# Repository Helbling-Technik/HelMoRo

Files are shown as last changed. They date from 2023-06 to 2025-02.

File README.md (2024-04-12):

# HelMoRo Hardware Repo

This repo includes all the Hardware files referenced on the Documentation Website.
You'll find the Website under [https://helbling-technik.github.io/HelMoRo/](https://helbling-technik.github.io/HelMoRo/)

Additionally all the Helmoro Documentation Markdown files that are used to produce the Documentation Webpage are stored here under the '/doc' folder.
There you'll find another [README.md](/docs/README.md) specifically about the website.

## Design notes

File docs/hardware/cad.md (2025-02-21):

# CAD 

## Downloads

In addition to the [Fusion 360 Widget ](https://helbling2.autodesk360.com/shares/public/SHd38bfQT1fb47330c99f726a386eb5b24d0) (HelMoRo with Raspberry Pi 5), we provide the model in the following formats:

- [Solidworks 2021](https://github.com/Helbling-Technik/HelMoRo/tree/master/cad/solidworks) 
- [STEP](https://github.com/Helbling-Technik/HelMoRo/tree/master/cad/step) 
- [STL](https://github.com/Helbling-Technik/HelMoRo/tree/master/cad/stl) 

Some files extend the file limit of 100 Mb, and therefore, we use [GitHub LFS](https://git-lfs.com/) (Large File Storage) to manage these large files effectively. Instructions how to use GitHub LFS can be found under [Collaboration](../../collaboration#accessing-the-repository).

## Naming Convention

The file names are in the following format:
**HEL-XX-UUYYY-RR.xyz**

- **HEL**: This prefix represents the client.
    <div style="margin-left: 20px;">
        <strong>&nbsp;&nbsp;&nbsp;HEL:</strong> Helbling (internal project)<br>
    </div>

- **XX**: This section indicates the type of the CAD file.
    <div style="margin-left: 20px;">
        <strong>&nbsp;&nbsp;&nbsp;01:</strong> Main assembly<br>
        <strong>&nbsp;&nbsp;&nbsp;03:</strong> Sub-assembly<br>
        <strong>&nbsp;&nbsp;&nbsp;04:</strong> Generative part or sheet metal<br>
        <strong>&nbsp;&nbsp;&nbsp;06:</strong> Purchased electronic part
    </div>

- **UU**: The creator of the part is specified here. User **01** up to **04** exist.

- **YYY**: The number of the part is composed of a three-digit code that starts from **000** and increments by one for each new part.

- **RR**: The revision number is a two-digit code that starts from **00** and increases with each subsequent revision of the CAD file.

- **xyz**: File type.
    <div style="margin-left: 20px;">
        <strong>&nbsp;&nbsp;&nbsp;sldsasm:</strong> SolidWorks assembly file<br>
        <strong>&nbsp;&nbsp;&nbsp;sldprt:</strong> SolidWorks part file<br>
        <strong>&nbsp;&nbsp;&nbsp;step:</strong> STEP file<br>
        <strong>&nbsp;&nbsp;&nbsp;stl:</strong> STL file<br>
    </div>

### Additional Notes

- The part number (**YYY**) resets to 000 for different part types (**XX**) and for each user (**UU**). For example, both HEL-04-01000-00 and HEL-06-01000-00 may exist as one is a generative part or sheet metal and the other is an electronic part.

- Fasteners, such as screws and nuts, do not have a part number.

### Example

**HEL-06-01000-01.sldprt**

- **HEL**: Helbling
- **06**: Purchased electronic part
- **01**: User 1
- **000**: Part number 0
- **000**: Revision number 1
- **sldprt**: SolidWorks part file

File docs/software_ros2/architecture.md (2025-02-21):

# Software Architecture
## High Level Overview
The following flowchart shows a high-level view of the communication in-between our packages when running the system on the robot. Naming convention in our repository may vary, as we show here the underlying algorithms of our packages, instead of the packages named by our internal company convention. In case of running the HelMoRo repository as a simulation, the four lefternmost hardware nodes are replaced by a single gazebo_ros bridge, which handles communication between ROS and the gazebo simulation engine. The internal packages are briefly explained in sections [helmoro_common](#helmoro_common), [helmoro_real](#helmoro_real) and [helmoro_sim](#helmoro_sim). External Packages are explained in section [External Packages](#external-packages). 

This image shows the high level communication between the our ROS packages High Level Communication

## helmoro_common

In the following, each package of the Helmoro ROS architecture is explained shortly.

### bringup
- manages the launch process of the HelMoRo
- manages the launch process of RVIZ

### control
- stores parameters for diff drive controller and joint state broadcaster.

### description
- stores URDF and meshes
- publishes static transforms

### state_estimation
- uses [robot_localization](http://docs.ros.org/en/melodic/api/robot_localization/html/index.html) in the background
- combines wheel odometry and IMU information with an EKF
- publishes transform between HelMoRo and odom frame

### slam
- uses [slam_toolbox](https://docs.ros.org/en/humble/p/slam_toolbox/) in the background
- combines lidar scans and odometry pose to create a map of the environment and localizes HelMoRo within
- publishes transform between map and odom frame

## helmoro_real
### bringup
- manages the launch process of packages interfacing with IMU, camera, LIDAR and motors

### motors
- ROS2 wrapper for the motor controllers
- converts motor states into wheel odometry
- converts robot velocity commands into motor commands

#### Wiring Options

|  | Checklist | |
|  |  |  |
| Wiring  |- Wire both RoboClaws to the Jetson Nano SBC via Micro-USB to Micro-USB cable. |
| Setting | - Connect one RoboClaw to PC via USB and open it with the downloaded [BasicmicroMotionStudio](https://www.basicmicro.com/downloads) <br>- Don’t set any of the two RoboClaws to USB-TTL Relay Mode <br>- Set an address for each RoboClaw in the General Settings. Note for this wiring, the addresses can be equal since ports are different (/dev/ttyACM0 and /dev/ttyACM1 in Linux) <br>- Set Baudrate you would like to use in the General Settings. <br>- [Configure the PID values](https://resources.basicmicro.com/auto-tuning-with-motion-studio) of the RoboClaws if not yet done. <br>- Don’t forget to Device &rarr; Write Settings in the top left corner before disconnecting your RoboClaw. |

## helmoro_sim
### bringup
- manages the launch process of the gazebo simulation and spawns the robot

### gazebo_tools
- contains world files
- starts the ros-gazebo bridge

## helmoro_operations
### joymanager
- interprets joystick commands from Logitech Wireless joystick F710 controller
- scales joystick commands to desired linear and angular velocities
- publishes of velocity commands

### navigation
- uses [navigation2](https://docs.nav2.org/) in the background
- launches nodes for local and global costmap generation
- launches nodes for recovery behaviour, planning and trajectory following

## External Packages

### Camera
The [OrbbecSDK ROS2 Wrapper](https://github.com/Helbling-Technik/HelMoRo_OrbbecSDK_ROS2) provides integration of Orbbec cameras with ROS 2 environment. It supports ROS2 Foxy, Humble, and Jazzy distributions. Helmoro's camera, the Astra Pro Plus, is EoL. We created our own fork to fix a bug caused by non-existing intrinsic parameters.

### IMU
The [bno055](https://github.com/flynneva/bno055.git) package is a community created packages for interfacing with the IMU Bosch BNO055 IMU.

### LIDAR
The [rplidar_ros](https://github.com/Slamtec/rplidar_ros) packages is provided by the LIDAR manufacturer Slamtec. It supports ROS1 and ROS2.

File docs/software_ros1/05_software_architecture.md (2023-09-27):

# Architectural Overview

The following flowchart shows an overview of the ROS architecture of Helmoro including internal and external packages when the parameter `is_real_robot` is set to true and gazebo is not running. The internal packages will be briefly explained in section [Packages](#packages). External Packages will be explained in section [Dependencies](#dependencies). Additionally, packages used for [SLAM](#slam-using-gmapping) (gmapping), [Autonomous Navigation](#autonomous-navigation-using-the-navigation-stack) (Nav Stack) and [Autonomous SLAM](#autonomous-slam-using-explore_lite) (explore_lite) are further explained in their respective sections.

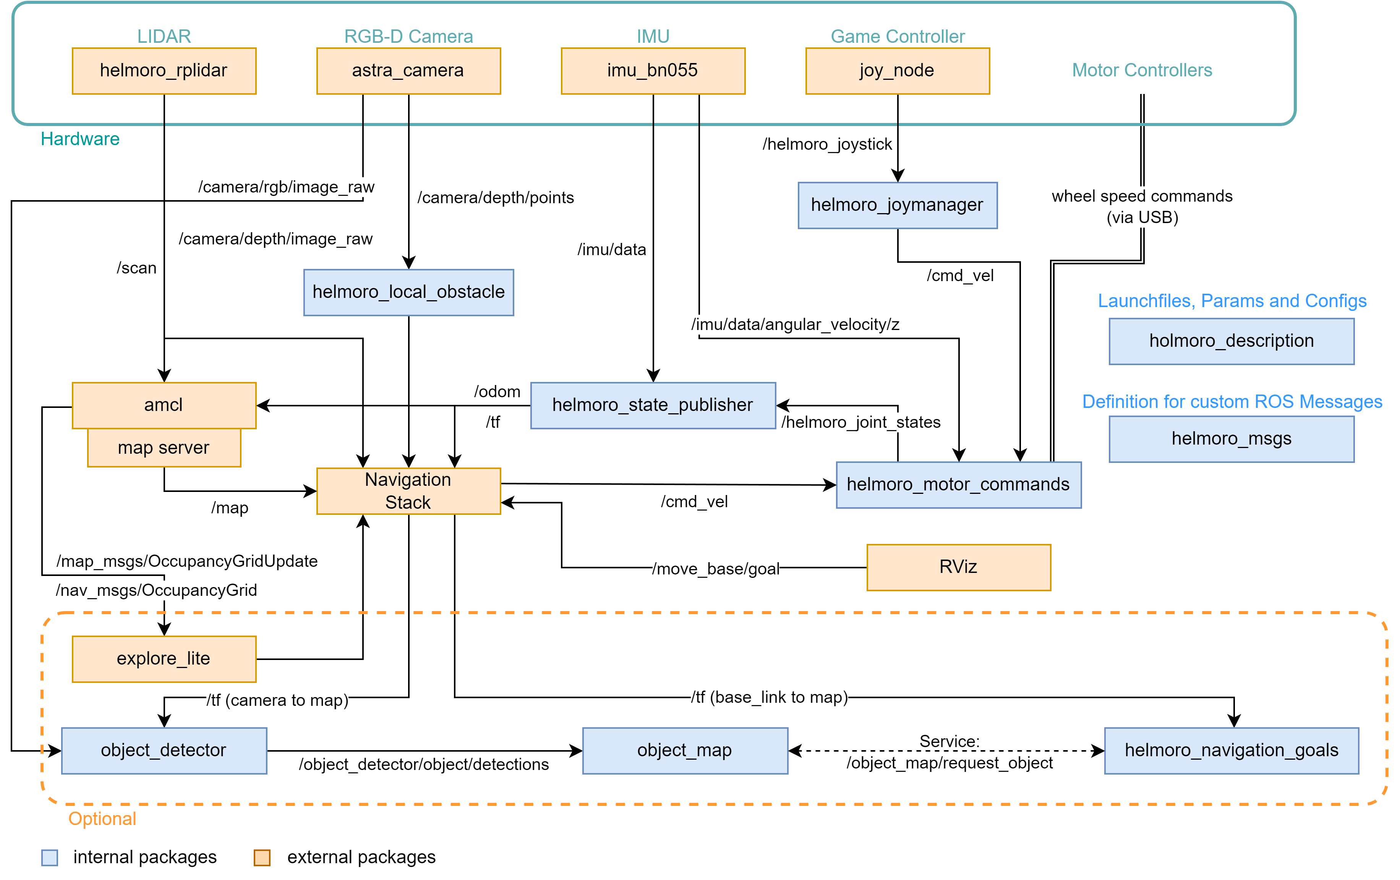
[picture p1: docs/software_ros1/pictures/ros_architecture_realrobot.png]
ros_architecture_realrobot


# Packages

In the following, each package of the Helmoro ROS architecture is explained shortly.

## helmoro_description

### launch files

- helmoro.launch: Main launch file, that starts all the required nodes for Helmoro.
- gmapping_helmoro.launch: Launch file for gmapping (for customizable parameters).

### param

- default.yaml stores Helmoro's hardware specs and is used by many different nodes.

### urdf and meshes

- Meshes and .urdf files are used for the physical description of Helmoro. They define orientation and position of the different hardware components to each other. This is used to build a robot model, that can be visualized in rviz, for tf information of the different frames that are published to `/tf` using helmoro_state_publisher and for the specification of the sensor streams that should be simulated in gazebo.

### rviz

- rviz_config.rviz: rviz config file, that describes the default rviz settings for Helmoro.

<!-- ## helmoro_msgs -->

Package where all the required custom messages and services for Helmoro are described.

## helmoro_joymanager

### launch files

- joymanager.launch: Calls the two nodes joy_node (remapped as helmoro_joystick) and helmoro_joymanager and loads the parameters described in parameters.yaml

### nodes

- joy_node: interprets the joystick commands coming from the Logitech Wireless joystick F710 controller and publishes them over a message of type [sensor_msgs/Joy](http://docs.ros.org/melodic/api/sensor_msgs/html/msg/Joy.html) to the topic `/helmoro_joystick`
- helmoro_joymanager_node: Subscribes to the `/helmoro_joystick` topic, scales the joystick commands and publishes a message of type [geometry_msgs/Twist](https://docs.ros.org/api/geometry_msgs/html/msg/Twist.html) on the topic `/cmd_vel` describing the desired linear and angular movement of the Helmoro.

## helmoro_motor_commands

The helmoro_motor_commands package is only used if `is_real_robot` is set to true and used for sending desired speed commands to the motor controllers and reading out the angular speeds and position coming from the encoders. Information on the setup of the RoboClaw Motor Controllers can be found here:

<center>

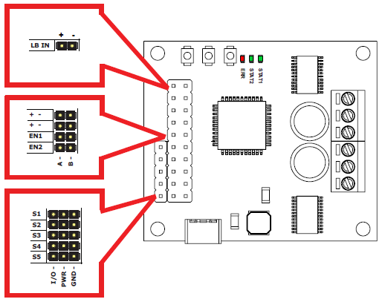
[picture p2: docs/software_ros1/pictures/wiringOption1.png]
Wiring Options


</center>

| | Option 1 | Option 2 |
| :--- | :--- | :--- |
| Wiring  | - Wire one of the two RoboClaws to the Jetson Nano SBC via Micro-USB to Micro-USB cable <br>- Wire the second RoboClaw to the first with UART. Don’t forget to connect the Ground and to Switch RX and TX. <br>- RoboClaw: RX on S1 pin, TX on S2 pin | - Wire both RoboClaws to the Jetson Nano SBC via Micro-USB to Micro-USB cable |
| Setting | - Connect one RoboClaw to PC via USB and open it with the [downloaded BasicmicroMotionStudio](https://www.basicmicro.com/downloads) <br>- Set first RoboClaw to USB-TTL Relay Mode in the General Settings <br>- Leave second RoboClaw as it is. No Multi-Unit Mode! <br>- Set a unique address for each RoboClaws in the General Settings in order for them not to conflict with each other <br>- Set Baudrate you would like to use in the General Settings <br>- [Configure the PID values](https://resources.basicmicro.com/auto-tuning-with-motion-studio) of the RoboClaws if not yet done. <br>- Don’t forget to Device $\rightarrow$ Write Settings in the top left corner before disconnecting your RoboClaw. | - Connect one RoboClaw to PC via USB and open it with the [downloaded BasicmicroMotionStudio](https://www.basicmicro.com/downloads) <br>- Don’t set any of the two RoboClaws to USB-TTL Relay Mode <br>- Set an address for each RoboClaw in the General Settings. Note for this wiring, the addresses can be equal since ports are different (/dev/ttyACM0 and /dev/ttyACM1 in Linux) <br>- Set Baudrate you would like to use in the General Settings <br>- [Configure the PID values](https://resources.basicmicro.com/auto-tuning-with-motion-studio)] of the RoboClaws if not yet done. <br>- Don’t forget to Device $\rightarrow$ Write Settings in the top left corner before disconnecting your RoboClaw |

### nodes

- helmoro_motor_commands: Subscribes to `/cmd_vel` and `/imu/data` and computes the desired wheel speed using a straight forward computation and an integral term that sums up the error between the desired and actual (imu measured) angular speed of Helmoro's base. It sends the computed speeds to the two motor controllers and in turn reads the wheel speeds and positions and publishes them as a custom message on `/helmoro_joint_states`. Messages are sent and read from the motor controllers using the functions defined under motor_interface. They actually imitate the functions from the [RoboClaw Python Library](https://resources.basicmicro.com/using-the-roboclaw-python-library/) for C++ usage. (see `motor_command_types.h` for the according command numbers and compare them to the numbers used in the python library or in `helmoro_roboclaw`).

### comments

- In order for commands to be sent and received at a high baudrate (such as the currently set value of 115200), both roboclaw motor controllers need to be connected to the Jetson Nano by USB since bits cannot be sent over serial connections at such a high rate without errors occurring in the data transmission process. If you want to cable your motor controllers differently, you can connect a USB cable to one of the two motor controllers and connect the second to the first via UART (remember to adjust the first Roboclaw motor controller to be in USB-TTL relay mode in the BasicMicro Motion Studio). For that setting however, the baudrate needs to be set to a lower value such as 38400 for the messages not to turn out erroneous. Bear in mind, that then the individual motor_interface functions will require more time and therefore the node might not be able to run at the same rate anymore, which then needs to be adjusted. Also, if you want to change to this setting, you will need to adjust the node so that only one motor_interface instance with one portname is created and only the address is varied to communicate with the left and right motor controller.

### troubleshooting

In case you are getting errors from this package and the Roboclaw Motor Controllers are not working, go through the following quick checks:

1. Check if the port name of both Roboclaws appear when plugin in, the USB by typing `ls /dev/ttyACM*`
2. Check if you have the authority to write to this port. Otherwise type `chmod 666 <portname>` in order to add the authority.
3. Also, when using this node with two USB cables, it can happen that the portnames of the left and the right roboclaw motor controller swap (`/dev/ttyACM0` <-> `/dev/ttyACM1`). Since, to this point their USB ports are not fixed. If this happens, simply swap the two addresses for the left and the right controller specified in the param file.

## helmoro_gazebo_plugin

This package is only used, when the argument `is_real_robot` in helmoro.launch is set to false. Package that is used to run the gazebo simulation.

### nodes

- helmoro_gazebo_plugin: Custom gazebo-plugin for the Helmoro, which simulates the wheel ground interaction.

### worlds

Built worlds in which gazebo simulation can be started.

## helmoro_state_publisher

### nodes

- helmoro_state_publisher_node: Subscribes to `/helmoro_joint_states` and `/imu/data` coming from an imu package called [imu_bno055](#ros_imu_bno055) (described under dependencies). The node computes the Helmoro odometry thereof and publishes it as a message of type [nav_msgs::Odometry](http://docs.ros.org/melodic/api/nav_msgs/html/msg/Odometry.html) onto the `/odom` and onto `/tf`. It also publishes the static transforms, defined in helmoro_description/urdf and the wheel positions of Helmoro onto `/tf`.

## helmoro_local_obstacle

### nodes

- helmoro_local_obstacle_node: Subscribes to the `/camera/depth/points` topic of message type [sensor_msgs/PointCloud2](http://docs.ros.org/melodic/api/sensor_msgs/html/msg/PointCloud2.html) coming from the [astra_camera](#ros_astra_camera) package which is described below. The node simply downsamples the incoming pointcloud using a VoxelGrid filter and publishes it as `/pointcloud_filtered`.

## helmoro_2dnav

This package holds all the used launch and parameter files for the custom usage of the Navigation Stack with Helmoro. For more information, head to Navstack section.

## object_detector

### Description

Helmoro can detect coloured cubic objects and locate them using its RGB-D camera Once detected, the location of these objects is saved into a map, so that they can be targeted by the navigation stack. The object_detector looks for colored boxes in an image and outputs their 3D position in the map frame. (included in showcase_helmoro.launch)

### Limitations

Since the object detection algorithm used mainly checks for colours, the lighting conditions strongly influence the performance of this task.

### nodes

- object_detector: Subscribes to `/camera/rgb/camera_info` for the camera intrinsics, `/camera/rgb/image_raw` for the color image to find the objects, `/camera/depth/image_raw` for the depth information when objects in the color image were found. Publishes a custom message to `object_detector/object_detections` that contains all found objects in the current image, their color and their 3D position in the map frame. For debugging purposes, an image is published to `object_detector/object_detections_image` that indicates with black dots all the objects that were found. 
You can have a look at it using 'rqt_image_view'.
  ```sh
  rosrun rqt_image_view rqt_image_view
  ```

## object_map

The object_map maintains a map of all detected objects. If a detection is made close to a previous detection, it fuses both measurements instead of creating a new one. The distance under which this happens is configurable in the parameter file. All objects in the map are assigned a unique identification number such that it one can easily refer to a specific object. It publishes a service, where it sends the most often seen object from a specific colour to the requester (`/object_map/request_object`) and a service with which it is possible to edit (currently only delete) a specific object (`/object_map/edit_map`).

### nodes

- object_map: Subscribes to `/object_detector/object_detections` for all current object detections. All objects are put in a map and assigned a unique id. If the object already exists, its position is updated using a filter. It publishes a service, where it sends the most often seen object from a specific colour to the requester (`/object_map/request_object`) and a service with which it is possible to edit (currently only delete) a specific object (`/object_map/edit_map`).

### comments

- The object map keeps track of the certainty of an object in an absolute way, meaning it tracks how often a specific object was send by the object_detector.
- In the current implementation, objects are never automatically removed from the map. One could think of removing objects if the Helmoro looks at an object for a long time, but does not see it.

## helmoro_navigation_goals

This package is used for sending navigation goals to the navigation stack based on the location of the detected objects from the object map. (included in showcase_helmoro.launch)

### nodes

- helmoro_navigation_goals: Requests new objects (with their location) from the map via a rosservice `/object_map/request_object` (type `RequestObjectFromMap.srv`) and commands the robot to collect them. It does that, by going through a simple State machine and sending the computed goals to the navigation stack using \_actionlib* (as described on this [ROS wiki](http://wiki.ros.org/navigation/Tutorials/SendingSimpleGoals)).
- The task to collect the objects after they are added to the map can be started by pushing the `start` button on the joystick controller.
- At all times, during the object collection task the `back` button on the joystick controller can be used to cancel the collection of the objects and the following of the trajectories.
- When Helmoro is prepared to pick up the object, this node requests the deletion of the collected object from the map with the ros service `/object_map/edit_map` (type: `EditObjectMap.srv`).
- When Helmoro picks the object up, he changes his minimum forward speed (`min_vel_x`) to a positive value (configurable). Like this it is ensured, that Helmoro does not drive backwards or rotates in place, as this could lead to the loss of the object. He also edits his own goal acceptance tolerance to ensure no endless rotations at the global_goal by changing `xy_goal_tolerance`(configurable). When Helmoro reaches the global goal and delivered the object he then reverts both values to their original value to be able to navigate normally. (The original values is configured in the param file of the DWAPlanner).
- Helmoro has two ways how to pick up an object. This can be specified by selection `target_mode` in the parameter file.
  - Target mode 1: Helmoro drives around the object and turns behind it. He then pushes it to the global_goal.
  - Target mode 2: Helmoro drives straight on to the object and then turns with it.

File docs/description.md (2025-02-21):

# Description
Explore the world of robotics with HelMoRo, a versatile four-wheeled robot designed by [Helbling](https://www.helbling.ch/en). With its user-friendly assembly process and state-of-the-art components, HelMoRo provides an exciting platform for robotics enthusiasts and professionals alike.

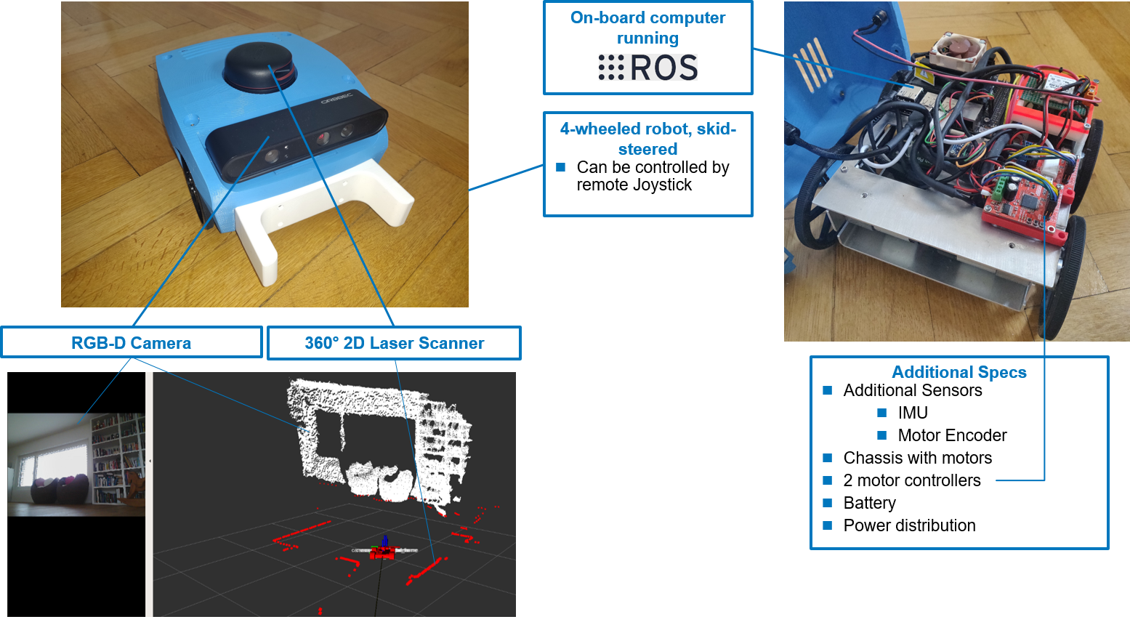
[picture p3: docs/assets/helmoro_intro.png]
helmoro_intro


## Key Features

- **Robust and Agile**: 
Built on a sturdy four-wheel chassis, its skid-steered navigation system with [Roboclaw Motor Controllers](https://www.basicmicro.com/Roboclaw-2x7A-Motor-Controller_p_55.html) offers ensures agile movement and precise control.
- **Advanced Sensing**: 
Equipped with sensors including [Slamtec RPlidar LIDAR](https://www.slamtec.com/en/Lidar/A2/) and an [Orbbec Astra Pro RGB-D Camera](https://shop.orbbec3d.com/Astra-Pro-Plus) and an [Adafruit BNO055 Absolut Orientation](https://learn.adafruit.com/adafruit-bno055-absolute-orientation-sensor) IMU Sensor, HelMoRo accurately perceives its surroundings to navigate and interact with its environment effectively.
- **Powerful Computing**: Powered by the [Raspberry Pi 5](https://www.raspberrypi.com/products/raspberry-pi-5/) running Ubuntu 22.04, HelMoRo handles complex data processing, supporting a variety of machine learning applications.

## Capabilities

- **Real-Time Monitoring**: Streams video, map, and positional data for remote monitoring and analysis.
- **Remote and Autonomous Control**: Easily controlled via a remote joystick or capable of autonomous navigation through advanced sensors for precise movement and obstacle avoidance.
- **Mapping and Detection**: Performs both remote-controlled and autonomous mapping, allowing it to create detailed environmental maps. Additionally, HelMoRo can detect and autonomously handle objects.

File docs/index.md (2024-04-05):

---
template: home.html
title: Home
---

<!-- ---
hide:
  - navigation
  - toc
--- -->

# Welcome to Helmoro

Welcome to the official documentation of **Helmoro**, the **Hel**bling **mo**bile **ro**bot. Helmoro is an open-source robotic platform designed by Helbling Technik in Zurich, Switzerland. 

It is equipped with LiDAR sensors and depth cameras, and thus is able to navigate autonomously. Additionally, we implemented a ROS node that allows the robot to be controlled with a game controller.

<iframe src="https://www.youtube.com/embed/QdNnvhEyrZk" title="YouTube video player" frameborder="0" allow="accelerometer; autoplay; clipboard-write; encrypted-media; gyroscope; picture-in-picture; web-share" allowfullscreen></iframe>

On this website, you will find a comprehensive guide designed to help you build your own mobile robot. 

Whether you are looking to get started with our software, interested in the technicalities of our hardware designs, or seeking detailed installation guides, you've come to the right place.

The website is structured into [Hardware Documentation](hardware/bill_of_materials.md) and [Software Documentation](software/01_software_introduction.md). 

In the Hardware section, you will find a complete list of materials, access to all CAD files, as well as the complete assembly instructions. 

In the Software section, you'll find a link to the repo containing all the source code as well as a complete guide on how to install and run all the packages. Additionally, we tried to explain the thoughts behind some of the algorithms.

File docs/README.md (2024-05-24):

# How to build website

## Installation

First install mkdocs using pip

```
pip install mkdocs 
```

Once installed, make sure to add the path to mkdocs to the systems environment variables. The installation process might print warnings about this already.
On windows this is found in *Advanced system settings* $\rightarrow$ *System Properties* $\rightarrow$ *Environment Variables*.
Look for the ``Path`` variable under *System variables* and check for the directory containing the mkdocs executable. If it does not exist add it to the ``Path`` variable.

Continue installing the following packages using pip

- table reader

  ```sh
  pip install mkdocs-table-reader-plugin 
  ```

- markdown include

  ```sh
  pip install markdown-include 
  ```

- mkdocs material

  ```sh
  pip install mkdocs-material
  ```

- openpyxl

  ```sh
  pip install openpyxl
  ```

## Run website locally

All configurations for the website are stored in the ``mkdocs.yml`` on the toplevel of the repo.

To run it locally simply run the following from the HelMoRo folder.

```
mkdocs serve -a localhost:8888
```

Make sure the port you are using is open.

Now the website can be accessed locally at http://localhost:8888

On Github within the Repo Settings under the Pages Tab you can access and change the published site preferences.

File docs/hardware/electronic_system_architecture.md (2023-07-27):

# Electronic System Architecture

The electronic system architecture diagram provides an overview of the system's components and their interconnections. The part numbers are the same as in the [Bill of Materials](bill_of_materials.md).

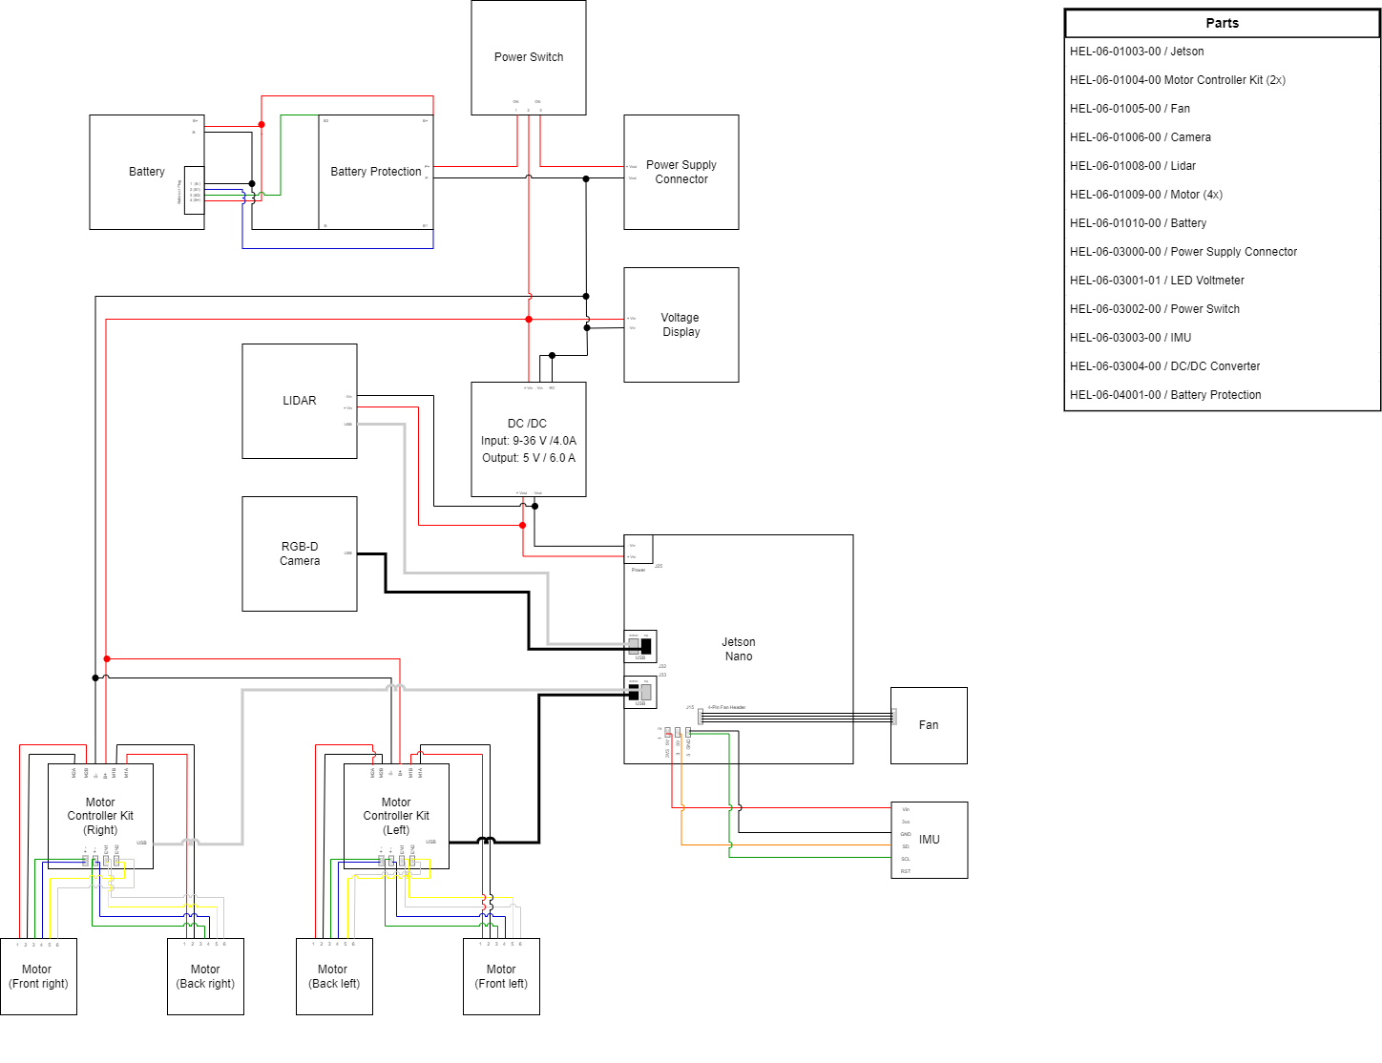
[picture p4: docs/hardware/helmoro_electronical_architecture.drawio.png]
Electronical architecture


[Download Electronical Architecture](Helmoro_Electronical_Architecture.pdf)

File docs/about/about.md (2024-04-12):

# About  

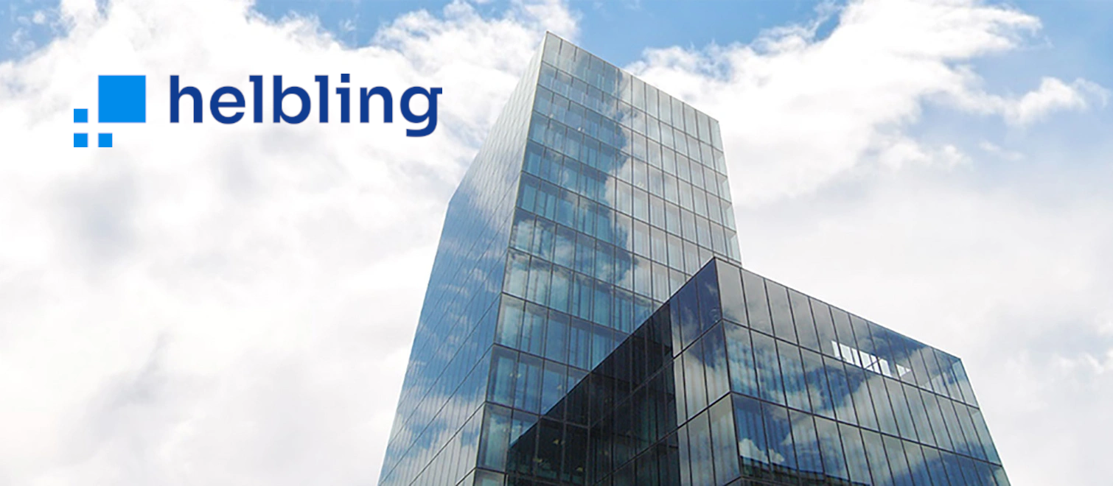
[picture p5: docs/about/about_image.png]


[Helbling](https://helbling.ch/en) is a globally active engineering and innovation partner supporting deep-tech product development from early ideation to industrialization with over 500 engineering specialists.
The passion for technology and problem-solving drives us to deliver cutting-edge products and services to our clients. Whether it's product design, prototyping, software development, or system integration, we excel in delivering high-quality solutions tailored to meet our clients' needs 

<div style="display: flex;">
  <div style="flex: 3; display: flex; flex-direction: column; justify-content: center; padding-left: 20px;">
    <b>Helbling Technik AG</b> <br>
    Hohlstrasse 614 <br>
    CH-8048 Zürich <br>
    +41 44 438 17 01 <br>
    info-htkz@helbling.ch
  </div>
  <div style="flex: 7; padding-left: 20px;">
    <iframe src="https://www.google.com/maps/embed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" width="100%" height="400" style="border:0;" allowfullscreen="" loading="lazy" referrerpolicy="no-referrer-when-downgrade"></iframe>
  </div>

</div>

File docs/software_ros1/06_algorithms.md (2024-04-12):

# High Level Algorithms

## SLAM using gmapping

Gmapping is a SLAM algorithm that can be used to generate a global map that can be used in autonomous navigation. It requires a horizontally fixed laser range finder(lidar) and subscribes to the `/scan` topic. Further it subscribes to `/tf` needing to know the transform between the lidar and the base_link and between the base_link and odom. In turn, it provides the transform between odom and the map frame to `/tf` and publishes the constantly updated map under the `/map` topic.

### Run

To create a map launch your helmoro in the desired environment (in gazebo or in real life)

```sh
roslaunch helmoro_description helmoro.launch
```

Open up a new terminal and enter

```sh
rosrun gmapping slam_gmapping scan:=scan
```

While this node is running drive around with your helmoro in the environment. This node will create a occupancy map using SLAM. When you are done driving around leave all the terminals running, open up a new one and enter

```sh
rosrun map_server map_saver -f <location and name of your_map>
```

This will create a your_map.pgm and your_map.yaml file at the location you defined. If you wish to use this map in navstack move it to the folder from which you call the maps and change the name of the map.yaml file in move_base.launch to your_map.yaml.

If you want to launch all commands together, you can just type

```sh
roslaunch helmoro_description gmapping_helmoro.launch
```

However, calling this custom launch file, you still need to run

```sh
rosrun map_server map_saver -f <location and name of your_map>
```

when you're finished.

### Configuration

Gmapping can be customized using parameters. The launch file **gmapping.launch**, which is saved under _helmoro_description/launch/gmapping_ calls the gmapping node with customized parameters for Helmoro. **helmoro_gmapping.launch** in turn calls **gmapping.launch** together with **helmoro.launch**.

### Limitations:

The gmapping algorithm only takes uses laser scan data coming from a horizontally mounted lidar. The RGB-D camera cannot be used for this task. Therefore, only objects that cross the "detection-plane" height of the lidar will be noticed. Also, highly reflective or transparent objects will not be detected properly using a lidar and will therefore not be written into the map.

### Troubleshooting

A problem often encountered when mapping feature poor environments such as long hallways, is that when driving the robot forward, it can skip back to the place it was before on the map since to gmapping, the features look alike. For this problem, it is advised to tweak the parameters so that gmapping puts more trust into the odometry information it gets. Have a look at [Bad maps produced by gmapping](https://answers.ros.org/question/189159/bad-maps-produced-by-gmapping-in-simulation-with-feature-poor-environments/) and [Repeated sideways jumps](https://answers.ros.org/question/193756/repeated-sideways-jumps-in-gmapping-with-hokuyo/) on ROS answer for further discussion on the topic.

For further information on the usage of gmapping head to: [gmapping ROS Wiki](http://wiki.ros.org/gmapping) and [slam_gmapping Tutorial](http://wiki.ros.org/slam_gmapping/Tutorials/MappingFromLoggedData)

## Autonomous Navigation using the Navigation Stack

72-autonomous-navigation-using-the-navigation-stack
For a good overview and detailed description head to:
[Navigation Stack ROS wiki](http://wiki.ros.org/navigation) and [Robot Setup](http://wiki.ros.org/navigation/Tutorials/RobotSetup)

### Concept

The following image shows a conceptual flowchart of the Navigation Stack. Note that the stack subscribes to exactly the blue topics that are provided by Helmoro.

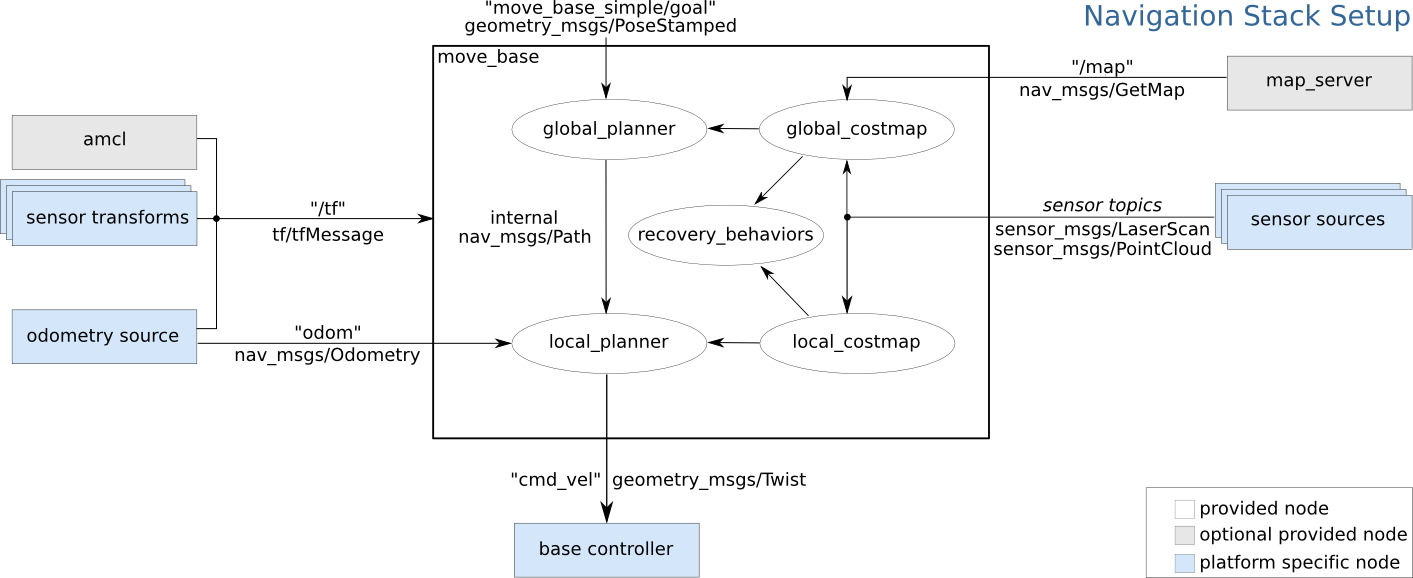
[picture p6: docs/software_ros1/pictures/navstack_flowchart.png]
navstack_flowchart


In short, a global goal (`/move_base_simple/goal`) can be sent to the navigation stack, which is interpreted by the global_planner. Taking into account information from the local and global costmap it will generate a path from the robot's current position to the global goal. This path is then interpreted by the local planner, which in turn publishes the movement command for the robot.

#### move_base

[move_base](http://wiki.ros.org/move_base) controls the different packages needed for autonomous navigation including a global and a local_costmap depending on [costmap_2d](http://wiki.ros.org/costmap_2d), a [global](http://wiki.ros.org/global_planner?distro=melodic) and a [local_planner](http://wiki.ros.org/base_local_planner?distro=melodic) and recovery behaviors. All the used packages for the navigation stack can be individually tuned using parameters. Refer to the links of the individual packages for further information.

#### map_server

If you want to hand over a global map to the Navigation Stack (created by gmapping), you can use the map_server by handing over the yaml file for the map you want to hand over. Note that the yaml file describes the location of the pgm file of your map.

#### AMCL

AMCL, short for Adaptive Monte Carlo Localization, takes in laser scans, odometry, tf and map provided by the map server and computes a pose estimate of the base_link w.r.t. the global map frame and publishes it onto `amcl_pose` and `/tf` topics. To do so, AMCL constantly compares information from the robot's odometry and the alignment of the laser scans with the global map. AMCL can be finetuned using parameters. For further information on AMCL, head to the [AMCL ROS wiki](http://wiki.ros.org/amcl).

### Configuration for Helmoro

The internal package helmoro_2dnav includes all the launch and parameter files used to for the specific application of the navigation stack to Helmoro.

The main launch file is ``move_base.launch``, which calls all the actions needed and reads in the parameters specified in the different parameter files.
It calls move_base:

```xml
<node pkg="move_base" type="move_base" respawn="false" name="move_base" output="screen">
```

as well as the map_server:

```xml
<node name="map_server" pkg="map_server" type="map_server" args="$(find helmoro_2dnav)/helmoro_maps/mymap.yaml"/>
```

and AMCL:

```xml
<include file="$(find helmoro_2dnav)/amcl_helmoro.launch" />
```

Further, the parameters used for Helmoro are specified in the following files:

- common_costmap_params: parameters for both local and global costmap
- local_costmap_params: parameters for the local costmap
- global_costmap_params: parameters for the global costmap
- base_local_planner_params: parameters for the local planner
- global_planner_params: parameters for the global planner

In addition, all maps used for the map server are saved in the folder _helmoro_2dnav/helmoro_maps_.

### Run

To run the navigation stack either set the value in the helmoro.launch file of 'use_nav_stack' to 'true' or type the following command into your terminal:
you can either call **helmoro.launch** and **move_base.launch** seperately:

```sh
roslaunch helmoro_description helmoro.launch
roslaunch helmoro_2dnav move_base.launch
```

or simply launch **nav_helmoro.launch**, which calls both above launch files together.

```sh
roslaunch helmoro_description nav_helmoro.launch
```

The navigation stack is easiest used in combination with RViZ where the different maps and paths of Helmoro's world can be visualized. You can send a goal using the `2D Nav Goal` button or place Helmoro at a distinct position in your map with the `2D Pose Estimate` button.
The settings to visualize the aspects of the navigation stack are saved in the default rviz config file under _helmoro_description/rviz/rviz_config.rviz_
Head to [Nav Stack with RViz](http://wiki.ros.org/navigation/Tutorials/Using%20rviz%20with%20the%20Navigation%20Stack) for further documentation on this topic.

You can also send goals and pose estimates directly in the terminal by typing:

```sh
rostopic pub -1 /move_base_simple/goal
```

or

```sh
rostopic pub -1 /initialpose
```

and tab-complete respectively.

If you repeatedly want to start Helmoro from the same position in your map and only want to go through the task of setting a matching map position for Helmoro in RViZ once, it's a good practise to first listen to the topic `/intitialpose` (`rostopic echo /initialpose`) in order to acquire the coordinates and to be able to set them through the terminal for the next start.

Another option to specify the start position of Helmoro is to specify it in the parameters `initial_pose_x`, `initial_pose_y` and `initial_pose_a` for AMCL. Currently, a launch file called **amcl_helmoro.launch** is called in **move_base.launch** as described in [configuration for helmoro](#configuration-for-helmoro).

In order to let Helmoro localize itself, you can use the `/global_localization` service offered by AMCL by typing:

```sh
rosservice call /global_localization "{}"
```

If Helmoro gets stuck and can't find a way out because of so called ghost objects (objects marked that are actually free space), try the following rosservice call:

```sh
rosservice call /move_base/clear_costmaps
```

For reference on this call, have a look at the following [ROS Answers](https://answers.ros.org/question/267485/local_costmap-ghost-objects-restarting-move_base/)

### Tuning the Navigation Stack

As mentioned above, the each functionality of the navigation stack can be finetuned using parameters. In the following, some suggestions and findings, that where made when tuning nav stack for Helmoro, on how to tune the parameters for the different functionalities are given. In addition, some useful links for tuning and troubleshooting the navigation stack are provided at the end of this subsection.

TIP: A lot of the parameters of the navigation stack are dynamically tunable. When you run 

``` sh
rosrun rqt_reconfigure rqt_reconfigure
```

while your robot is running you can change many values dynamically in runtime.

#### Costmaps in General

Both the local costmap and the global costmaps are two map types derived from [costmap_2d](http://wiki.ros.org/costmap_2d), which provides a configurable structure that maintains information about where the robot should navigate in the form of an occupancy grid. The difference between the two is that the global costmap is seeded with a user-generated static map (map server) and the local costmap has a specified width and height which keeps the robot centered inside it.

The costmaps can be configured using plugins for the different layers. The most commonly used layers are the static_layer (for the global costmap), the obstacle layer (tracks obstacles), inflation layer (lays inflation around obstacles). Obviously, the static layer should only be present in the global costmap. The local costmap in turn should have the parameter "rolling window" set to true. Have a look at global_costmap_params and local_costmap_params.

#### common_costmap_params

important obstacle_layer parameters:

- `max_obstacle_height`): The maximum height of any obstacle to be inserted into the costmap in meters. This parameter should be set to be slightly higher than the height of your robot. Can be over-ridden on a per-sensor basis.
- `obstacle_range`: Maximum distance from the robot at which an obstacle will be inserted into the cost map in meters. Can be over-ridden on a per-sensor basis. Have a look at the sensor specs to define this parameter.
- `raytrace_range`: The default range in meters at which to raytrace out obstacles from the map using sensor data. Set this parameter to a slightly higher value than obstacle_range to avoid ghost objects. Have a look at the sensor specs to define this parameter.

Further, you can define several sensor sources that are taken into account such as our rgb-d camera and lidar which in turn are configurable. Note that is important to set the parameter `inf_is_valid` to true for our lidar. The rplidar returns inf for invalid measurements for example when there is no object where the laser beam can reflect on in its range. This parameter will help raytrace objects from the costmap even if the laser beam is not reflected properly in a certain direction.

important inflation_layer parameters:

- `inflation_radius`: radius in meters to which the map inflates obstacle cost values. This parameter should be bigger that the circumscribed radius of the robot in order to guarantee robust navigation.
- `cost_scaling_factor`: rate ad which the exponential decay function of cost values away from an object drops. A higher value for this parameter will result in decreased cost values.

#### base_local_planner_params

Velocity and Acceleration:
It is important to set the minimal velocities to a value that lets Helmoro overcome friction and the maximal velocities so that Helmoro is able to reach them.
The easiest way to find the mathcing values for these parameters is to start the helmoro.launch file (without the navigation stack) and send a `/cmd_vel` to Helmoro directly through the terminal using

```sh
rostopic pub -r 50 /cmd_vel
```

and tab-complete. Simultaneously rqt_plot can be started and the desired topics can be displayed so that one can easily see how well Helmoro tracks a given `/cmd_vel`. For linear motion you would want to display `/odom/twist/twist/linear/x` and `/cmd_vel/linear/x`, for angular motion you would want to display `/odom/twist/twist/angular/z` and `/cmd_vel/angular/z`.

Goal distance tolerance:

- `xy_goal_tolerance`: Tolerance in meters in x and y direction for a goal to be considered reached.
- `yaw_goal_tolerance`: Tolerance in radians in yaw orientation for a goal to be considered reached.

Setting these parameters, the minimal linear and angular velocities mentioned above should be considered. A robot with a higher minimal velocity should be given a higher tolerance on its goal.

Forward simulation:

- `sim_time`: Defines the amount of time to forward simulate trajectories in seconds. This largely influences the behaviour of the robot especially when its close to reaching its goal. From experience, it is advised to keep this parameter between 1 and 2 seconds for Helmoro. The longer the value for `sim_time`, the higher the computational load becomes. However, setting `sim_time` too low, can result in limited performance especially when the robot needs to pass a narrow path. Another point is that forwardsimulated trajectories simulated are scored by their endpoints. Therefore, the `sim_time` parameter can have a large effect on how the robot behaves especially when its close to reaching its goal. For example if `min_vel_x` is set to 0.1m/s and `sim_time` is set to 5s, any trajectory with positive x velocity will move at least 0.5 meters forward. If now the goal tolerance is too low, in place rotations will score more favourably than a simple linear motion. A reasonable suggestion that can be looked up on this [ROS wiki](http://wiki.ros.org/navigation/Tutorials/Navigation%20Tuning%20Guide) page about tuning in section 3, is to set the parameters in the following fashion:
  - `min_vel_x * sim_time < 2 * xy_goal_tolerance`
  - `min_in_place_vel_theta * sim_time < 2 * yaw_goal_tolerance`

Bear in mind that a lot of parameters depend on each other. For example when lowering your value for sim_time, you may want to lower your value for path_distance_bias a little.

#### global_planner_params

The three most important parameters that influence the fashion how the global path is planned obtaining costmap information are `lethal_cost`, `neutral_cost` and `cost_factor`. These parameters have been left to default for Helmoro. For your reference, head to [Navguide](http://kaiyuzheng.me/documents/navguide.pdf) for a good explanation on these parameters.

#### Useful Links

In order to get an idea on how to tune parameters for the navigation stack, have a look at the following links:

Guides:

- [Navguide](http://kaiyuzheng.me/documents/navguide.pdf)

- [Navigation Tuning Guide](http://wiki.ros.org/navigation/Tutorials/Navigation%20Tuning%20Guide)

Examples:

- [Husarion Docs](https://husarion.com/tutorials/ros-tutorials/7-path-planning/)

- [caltech_samaritan](https://github.com/TimboKZ/caltech_samaritan/tree/master/param)

Troubleshooting:

- [ROS wiki troubleshooting](http://wiki.ros.org/navigation/Troubleshooting)

### Issues concerning the Navigation Stack

The Issues can be found under the [Issues](https://github.com/Helbling-Technik/HelMoRo/issues) of the repository

## Autonomous SLAM using explore_lite

### Concept

Helmoro can do the task of building a map autonomously using a ROS package called explore_lite.This package provides greedy frontier-based exploration. When node is running, robot will greedily explore its environment until no frontiers could be found. The following picture shows an intuitive overview of how the package works.

explore_lite

explore_lite sends different goal positions to the navigation stack considering the continuously updated map from gmapping or the costmap from move_base. Note that you can use both. Depending on your environment you may achieve better results with either SLAM map or costmap published by move_base. Advantage of move_base costmap is the inflation which helps to deal with some very small unexplorable frontiers. When you are using a raw map produced by SLAM you should set the min_frontier_size parameter to some reasonable number to deal with the small frontiers.

### Run

In order to Run the autonomous mapping task, run Helmoro with the Navigation Stack using gmapping instead of amcl. Also, make sure not to provide a map using the map_server. To do so, you can call the custom launch file for Helmoro called **explore_helmoro.launch**

```sh
roslaunch helmoro_description explore_helmoro.launch
```

Note that this launch file includes an argument `use_movebase_costmap`. If set to false, the launch file will call expore.launch, the launch file which will make explore*lite use map information from gmapping for planning. If set to true, the launch file will call expore_costmap.launch, the launch file which will make explore_lite use map information from the move_base costmap for planning. Both explore.launch and explore costmap.launch are saved under */helmoro*description/launch/explore_lite/* and hold custom parameters for the usage of explore_lite with Helmoro. If using explore_costmap.launch, it is very important to set the parameter `track_unknown_space` to true in **common_costmap_params.yaml** for the navigation stack.

Head to [explore_lite wiki](http://wiki.ros.org/explore_lite) for futher information. For an example and some helpful instructions, head to [Husarion Docs](https://husarion.com/tutorials/ros-tutorials/8-unknown-environment-exploration/).

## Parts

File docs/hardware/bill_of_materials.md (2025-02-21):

# Bill of Materials

All components of HelMoRo are listed below and structured in Electronic Parst, Generative Parts meaning those require a 3D printer, sheet metal parts that can be ordered from a workshop and all the needed fasteners. 
The Bill of Materials should be used to order all the parts before starting the assembly process.

Be aware that the **total estimated costs** of all parts of Helmoro are approximately: **1500.- Fr.**

Hint: Use the model-browser in the widget to search for a specific part name ([naming convention](../cad#naming-convention)). The widget shows the HelMoRo variant equipped with a Raspberry Pi 5, though the onboard computer could be assembled with a Jetson Nano too.

<iframe src="https://helbling2.autodesk360.com/shares/public/SHd38bfQT1fb47330c99f726a386eb5b24d0?mode=embed" width="1024" height="768" allowfullscreen="true" webkitallowfullscreen="true" mozallowfullscreen="true"  frameborder="0"></iframe>

## Electronics

{{ read_excel('./Helmoro_BoM_electronics.xlsx', engine='openpyxl', sheet_name="BoM") }}

## Generative Parts

{{ read_excel('./Helmoro_BoM_generative_parts.xlsx', engine='openpyxl', sheet_name="BoM") }}

## Sheet Metals

{{ read_excel('./Helmoro_BoM_sheet_metals.xlsx', engine='openpyxl', sheet_name="BoM") }}

The Top Plate can be ordered with the Clamping Nuts already pressed in.

## Fasteners

{{ read_excel('./Helmoro_BoM_fasteners.xlsx', engine='openpyxl', sheet_name="BoM") }}

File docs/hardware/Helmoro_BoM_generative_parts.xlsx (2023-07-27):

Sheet: BoM
QTY | NAME | DESCRIPTION | PRODUCT CODE | SUPPLIER | PRICE PER UNIT (CHF)
2 | Filament | Filament for Hull | Basf Filament, Digitec: 8817347 | [Digitec](https://www.digitec.ch/de/s1/product/basf-filament-pla-285-mm-750-g-3d-filament-8817347) | 30
1 | HEL-04-01004-00 | Battery Holder |  | Helbling 3D Printer
1 | HEL-04-01009-01 | Motor Controller Plate |  | Lasercutter
1 | HEL-04-01013-02 | Camera Plate |  | Helbling 3D Printer
1 | HEL-04-01017-01 | Holder Motor Controller |  | Helbling 3D Printer
1 | HEL-04-02001-00 | iPad holder |  | Helbling 3D Printer
4 | HEL-04-03000-01 | Wheel Cap |  | Helbling 3D Printer
1 | HEL-04-03001-00 | Body |  | Helbling 3D Printer
1 | HEL-04-03002-00 | Front Part |  | Helbling 3D Printer | 50
1 | HEL-04-03003-00 | Front Part with Fork |  | Helbling 3D Printer | 50
1 | HEL-04-03004-00 | Base Plate for Jetson |  | Lasercutter
1 | HEL-04-04000-00 | Circuit Board Holder Base |  | Helbling 3D Printer
1 | HEL-04-04001-00 | Circuit Board Holder Middle |  | Helbling 3D Printer
1 | HEL-04-04002-00 | Circuit Board Holder Top |  | Lasercutter

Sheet: Cabling
Item | Turck Part Number | Length [m] | QTY to ZHR | QTY to BOS | TOTAL QTY | Cost/part [CHF] | Total [CHF]
Total |  |  |  |  |  |  | 0

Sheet: Sheet2
Order Status
Open
Open AR
Ordered Helbling
Ordered AR
Available
n/a
Quote requested

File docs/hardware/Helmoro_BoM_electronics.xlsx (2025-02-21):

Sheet: BoM
QTY | NAME | DESCRIPTION | PRODUCT CODE | SUPPLIER | PRICE PER UNIT (CHF)
1 | Battery Cable | EP Silicone Cable 0.5mm² | EP Silicone Cable 0.5mm², red/black per 1m, 6059948 | [Digitec](https://www.digitec.ch/de/s1/product/ep-silikonlitze-rc-kabel-stecker-6059948) | 6
2 | Battery Connector | Deans M/F | EP Deans Connector, 6058001 | [Digitec](https://www.digitec.ch/en/s1/product/ep-deans-connector-rc-cables-plugs-6058001) | 11
4 | HEL-06-01000-01 | Wheel | pololu-wheel-90x10mm- black (4935) | [Robotshop](https://www.pololu.com/product/4935/) | 3
4 | HEL-06-01002-00 | Wheel Adapter | Pololu 1083 | [Robotshop](https://www.pololu.com/product/1083) | 4
1 | HEL-06-01003-00 | Jetson | 02110268 - NVIDIA® Jetson Nano™ Entwicklerkit | [Distrelec](https://www.sparkfun.com/products/16271) | 113
2 | HEL-06-01004-00 | Motor Controller Kit | RoboClaw IMC404 | [Robotshop](https://www.basicmicro.com/Roboclaw-2x7A-Motor-Controller_p_55.html) | 70
1 | HEL-06-01005-00 | Fan | Gehäuselüfter Noctua NF-A4x10 FLX | [Brack](https://www.brack.ch/noctua-pc-luefter-nf-a4x10-flx-223277) | 15
1 | HEL-06-01006-00 | Camera | ASTRA PRO Orbbec3D Astra Pro | [Reichelt](https://www.reichelt.de/de/de/orbbec3d-astra-pro-astra-pro-p263247.html?r=1) | 200
1 | HEL-06-01007-00 | LIDAR Adapter | Comes with LIDAR
1 | HEL-06-01008-00 | LIDAR | RPLIDAR A2M8 360° Laser Scanner | [Robotshop](https://www.robotshop.com/products/rplidar-a2m8-360-laser-scanner) | 320
4 | HEL-06-01009-00 | Motor | FIT 0186 | [Robotshop](https://eu.robotshop.com/de/products/12v-dc-motor-251rpm-encoder) | 30
1 | HEL-06-01010-00 | Battery | Swaytronic HC 3S 7200 mAh | [Galaxus](https://www.galaxus.ch/de/s5/product/swaytronic-hc-3s-1110-v-7200-mah-rc-akku-12400744) | 71
1 | HEL-06-01011-00 | Raspberry Pi 5 | Raspberry Pi 5 8GB | [Digitec](https://www.digitec.ch/de/s1/product/raspberry-pi-5-8gb-entwicklungsboard-kit-38955607?campaignid=16472930352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 | 86
1 | HEL-06-03000-00 | Power Supply Connector | 1614 21 - Netzgeräte-Einbaukupplung 5.4 x 8mm, Gerade, Lumberg | [Distrelec](https://www.distrelec.ch/de/netzgera-te-einbaukupplung-8mm-gerade-lumberg-connect-gmbh-1614-21/p/30068403) | 5
1 | HEL-06-03001-01 | LED Voltmeter (0.28" LED Digital DC Voltmeter 2.5VDC - 30VDC) | RB-Spa-1481 / PRT-14313 | [Robotshop](https://www.robotshop.com/products/028-led-digital-dc-voltmeter-spa) | 2
1 | HEL-06-03002-00 | Power Switch (Miniature Toggle Switch ON-OFF Latching) | RND 210-00494, Distrilec: 301-03-469 | [Distrilec](https://www.distrelec.ch/de/miniatur-kippschalter-ein-ein-rastend-wechsler-rnd-components-rnd-210-00494/p/30103469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 | 3
1 | HEL-06-03003-00 | IMU | 2472 - IMU, Distrelec: 300-91-187 | [Distrelec](https://www.distrelec.ch/en/dof-absolute-orientation-imu-fusion-breakout-3v-adafruit-2472/p/30091187) | 39
1 | HEL-06-03004-00 | DC/DC Converter | 30W 5V 6A, Distrelec: 301-45-575 | [Distrelec](https://www.distrelec.ch/en/dc-dc-converter-36v-5v-6a-30w-tdk-lambda-ccg-30-24-05s/p/30145575) | 38
2 | HEL-06-03005-00 | USB A-Connector - USB Micro-B-Connector | RND 765-00053, Distrilec: 301-25-761 | [Distrelec](https://www.distrelec.ch/de/usb-kabel-usb-stecker-usb-micro-stecker-500mm-usb-schwarz-rnd-connect-rnd-765-00053/p/30125761) | 2
1 | HEL-06-04000-00 | Prototyping Board for DC/DC Converter |  | [Robotshop](https://eu.robotshop.com/de/products/prototyping-board-7x10cm) | 6
1 | HEL-06-04001-00 | Battery Protection | hx-3s-fl25a-a | [Phipps](https://www.phippselectronics.com/product/hx-3s-fl25a-li-ion-18650-battery-protection-bms-board-3s-25a/), Alternative: [Robotshop](https://eu.robotshop.com/de/products/18650-battery-protection-module-12v-10a) | 13

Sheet: Cabling
Item | Turck Part Number | Length [m] | QTY to ZHR | QTY to BOS | TOTAL QTY | Cost/part [CHF] | Total [CHF]
Total |  |  |  |  |  |  | 0

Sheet: Sheet2
Order Status
Open
Open AR
Ordered Helbling
Ordered AR
Available
n/a
Quote requested

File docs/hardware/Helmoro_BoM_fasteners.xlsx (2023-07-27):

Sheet: BoM
QTY | NAME | DESCRIPTION | PRODUCT CODE | SUPPLIER | PRICE PER UNIT (CHF)
6 | DIN 7984 - M3 x 12 --- 10.5N | Screw M3x12 |  | Stock
4 | DIN 7984 - M3 x 18 - | Screws M3x18 |  | Stock
60 | DIN 7984 - M3 x 8 --- 6.5N | Screw M3x8 |  | Stock
2 | DIN 7985A - M2x5 | Screw M2x5 |  | Stock
2 | ISO - 4032 - M2 - D - N | Nut M2 |  | Stock
4 | ISO - 4032 - M2.5 - D - N | Nut M 2.5 |  | Stock
4 | ISO 14581 M2.5x16x16- | Screw M2.5x16 |  | Stock
4 | ISO 4762 M2 x 6 - 6N | Screws M2x6 | ISO 4762, Bossard Nr: 3 | Stock
9 | ISO 4762 M3 x 30 | Screw M3x30 |  | Stock
4 | ISO 4762 M3 x 40 | Screw M3x40 |  | Stock
2 | ISO 4762 M3x4 | Screw M3x4 | ISO 4762, Bossard Nr: 3 | [Bossard](https://www.bossard.com/eshop/ch-en/screws/screws-and-bolts-with-internal-drive/hex-socket-head-cap-screws-fully-threaded/p/3/)
12 | PEM CLA-M3-1 ---N | Clamping Nut (Pressed into Top Plate) |  | [Schickli](https://www.schickli.ch/)
12 | Thread Insert MULTISERT 003M3 | Threaded Bush | Gewindebuchsen für Kunststoffe 003-M3 | [kvt-fastening](https://shop.kvt-fastening.at/de/item/003M3.html) | 3
4 | Washer ISO 7092 - 2 | Washer M2 |  | Stock

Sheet: Cabling
Item | Turck Part Number | Length [m] | QTY to ZHR | QTY to BOS | TOTAL QTY | Cost/part [CHF] | Total [CHF]
Total |  |  |  |  |  |  | 0

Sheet: Sheet2
Order Status
Open
Open AR
Ordered Helbling
Ordered AR
Available
n/a
Quote requested

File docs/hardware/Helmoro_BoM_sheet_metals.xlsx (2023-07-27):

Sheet: BoM
QTY | NAME | DESCRIPTION | PRODUCT CODE | SUPPLIER | PRICE PER UNIT (CHF)
1 | HEL-04-01000-02 | Frame Mount |  | [Schickli](https://www.schickli.ch/) | 100
1 | HEL-04-01010-01 | Top Plate |  | [Schickli](https://www.schickli.ch/) | 80

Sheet: Cabling
Item | Turck Part Number | Length [m] | QTY to ZHR | QTY to BOS | TOTAL QTY | Cost/part [CHF] | Total [CHF]
Total |  |  |  |  |  |  | 0

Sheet: Sheet2
Order Status
Open
Open AR
Ordered Helbling
Ordered AR
Available
n/a
Quote requested

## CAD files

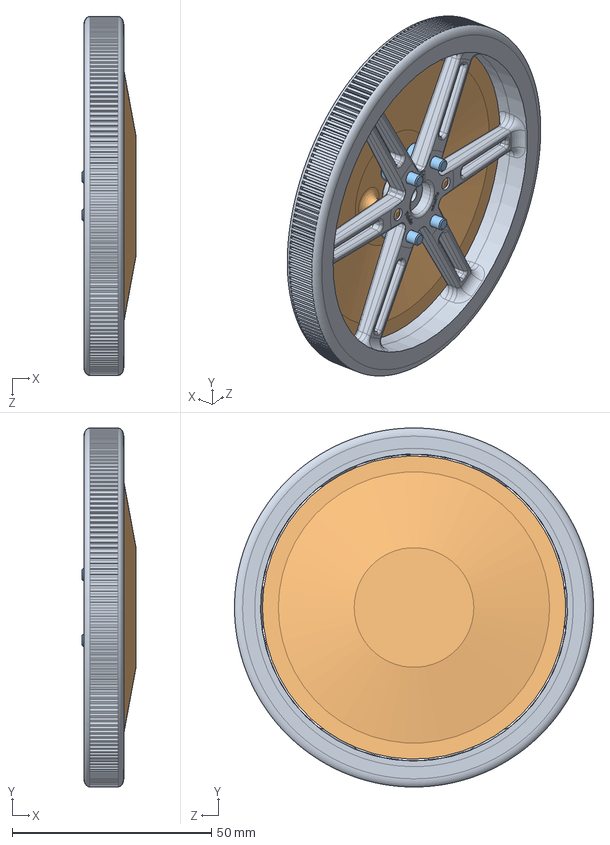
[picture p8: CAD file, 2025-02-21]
cad/solidworks 2023/HEL-03-01001-00.SLDASM
13.6 x 90.0 x 90.0 mm
HEL-06-01000-01
HEL-04-03000-01
socket head thin cap screw_din x 4

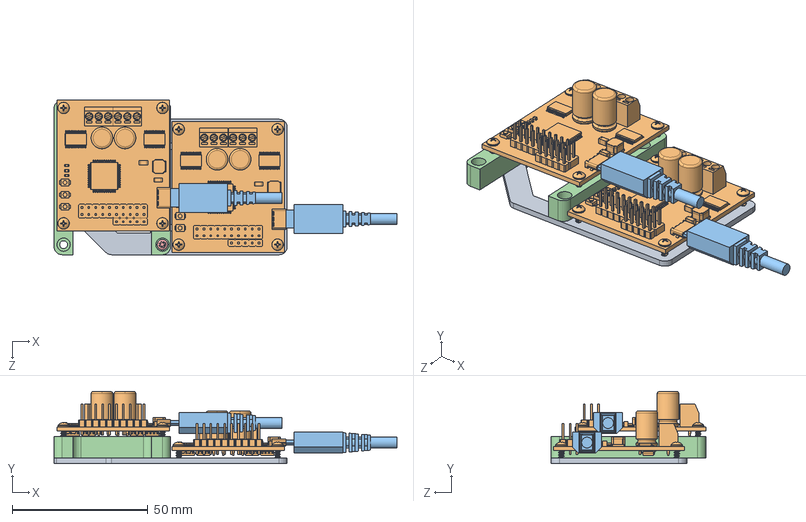
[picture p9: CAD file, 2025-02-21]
cad/solidworks 2023/HEL-03-01006-00.SLDASM
126.5 x 26.6 x 57.0 mm
HEL-04-01009-01
HEL-06-01004-00 x 2
HEL-06-03005-00 x 2
HEL-04-01017-01
Screw from Motor Controller Kit x 3

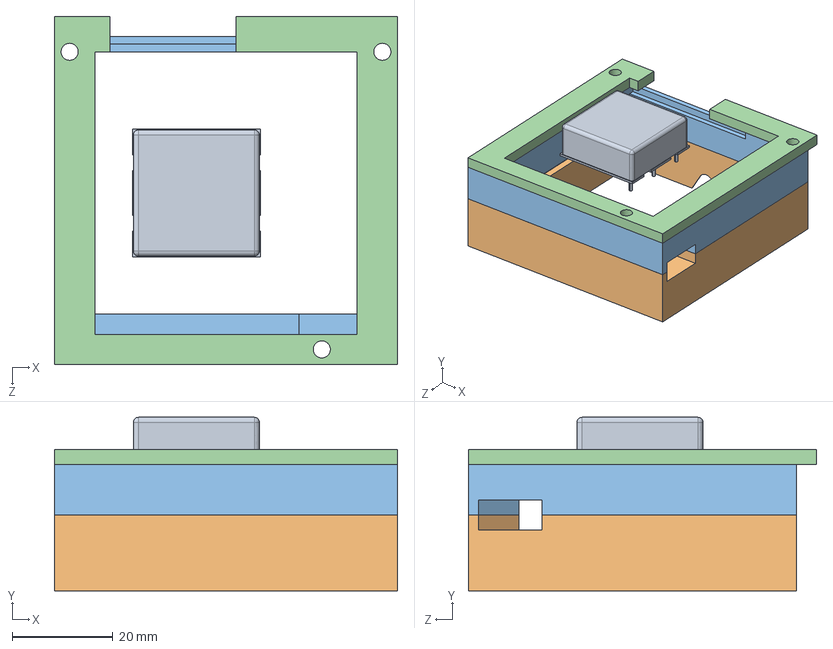
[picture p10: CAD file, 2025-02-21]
cad/solidworks 2023/HEL-03-03000-00.SLDASM
68.0 x 34.4 x 69.0 mm
HEL-06-03004-00
HEL-04-04000-00
HEL-04-04001-00
HEL-04-04002-00

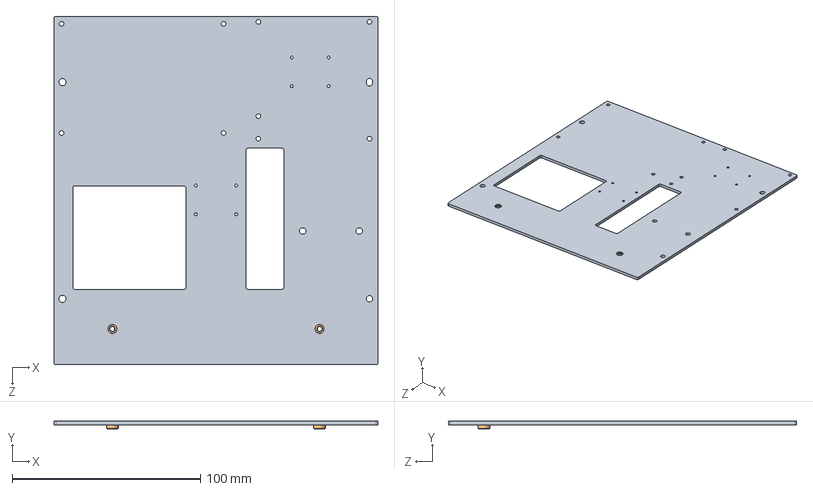
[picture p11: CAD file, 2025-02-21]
cad/solidworks 2023/HEL-03-01010-00.SLDASM
172.0 x 4.00 x 185.0 mm
HEL-04-01010-01
aluminum nut_pmm x 2

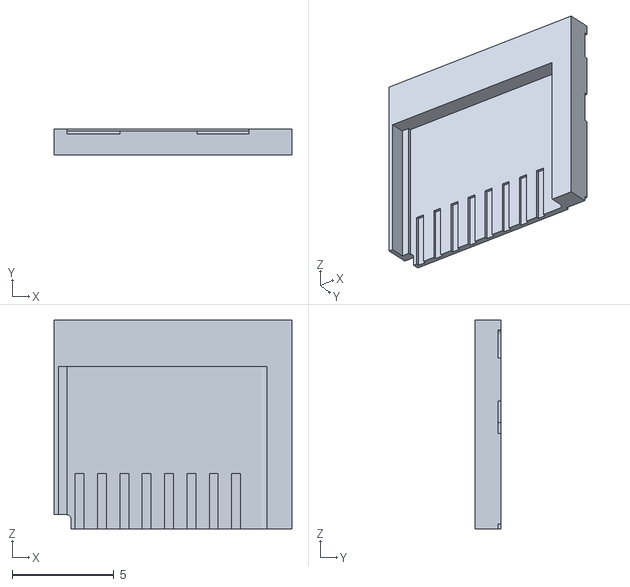
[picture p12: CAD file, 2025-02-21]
cad/stl/HEL-01-01000-02 - HEL-06-01011-00.STEP-1 RASPBERRY_PI_5_1.STEP_1.STEP-1 SLOT_CARD_ASM.STEP_1.STEP-1 SD_CARD_V1.STEP_1.STEP-1.STL
11.7 x 1.30 x 10.3

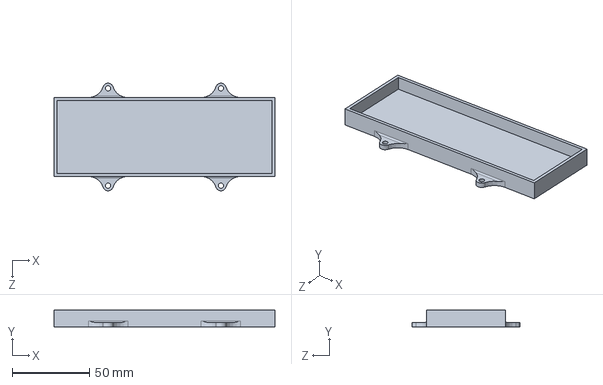
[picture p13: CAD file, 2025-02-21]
cad/solidworks 2023/HEL-03-01003-00.SLDASM
143.0 x 11.0 x 69.7 mm

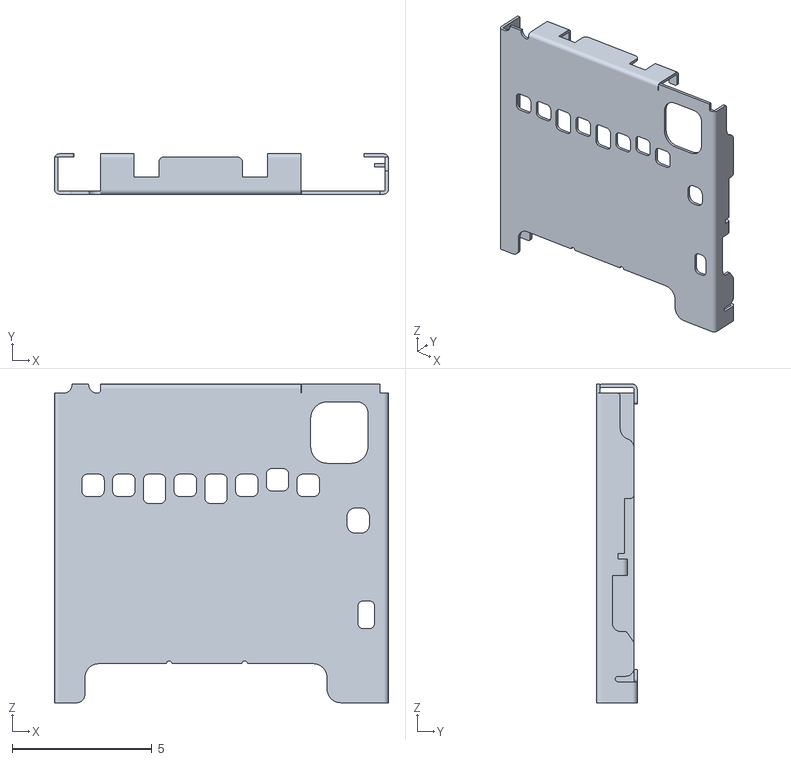
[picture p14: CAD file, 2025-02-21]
cad/stl/HEL-01-01000-02 - HEL-06-01011-00.STEP-1 RASPBERRY_PI_5_1.STEP_1.STEP-1 SLOT_CARD_ASM.STEP_1.STEP-1 PART3_V1.STEP_1.STEP-1.STL
12.0 x 1.45 x 11.4

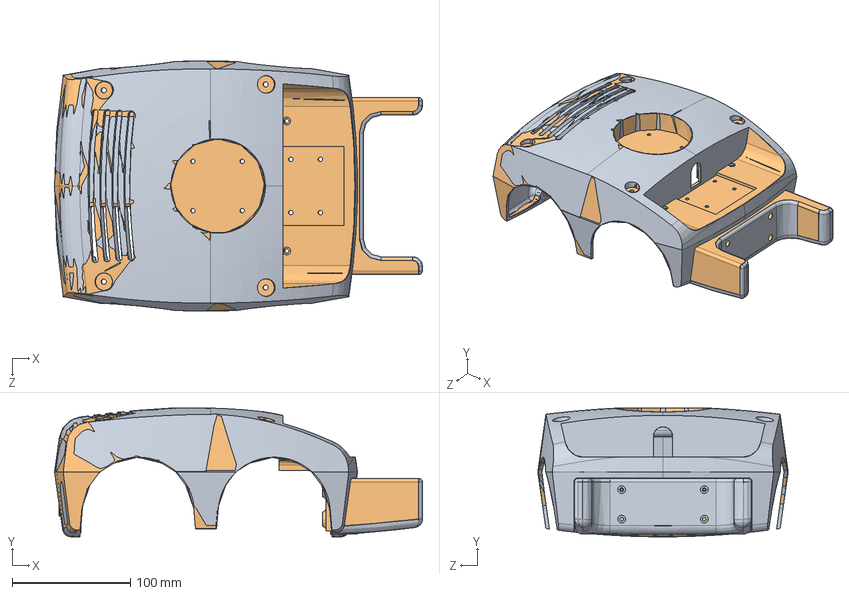
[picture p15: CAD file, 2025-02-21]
cad/solidworks 2023/HEL-03-01012-00.SLDASM
311.5 x 109.0 x 212.0 mm
HEL-04-03001-00
HEL-04-03002-00
socket head thin cap screw_din x 2
HEL-06-03000-00

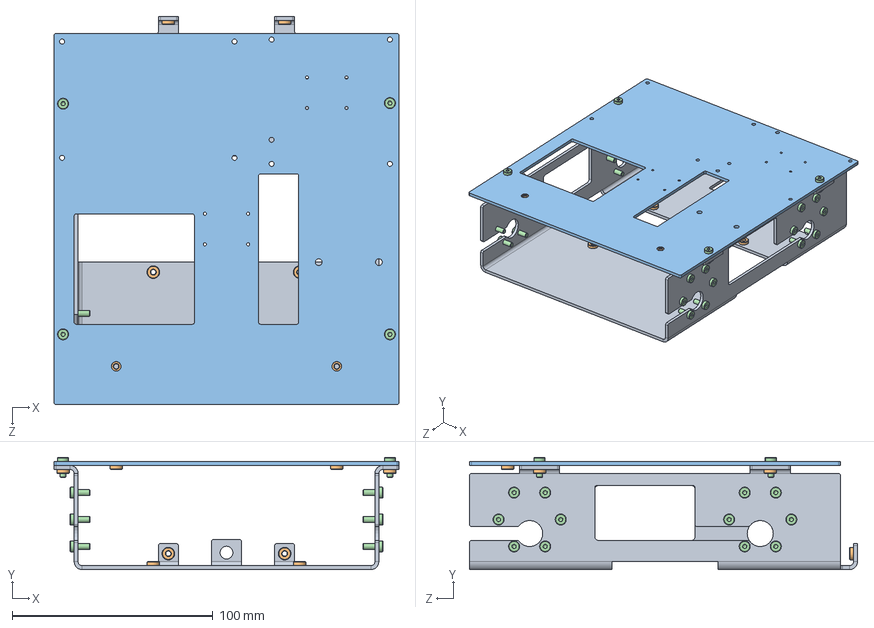
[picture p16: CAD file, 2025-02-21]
cad/solidworks 2023/HEL-03-01007-00.SLDASM
172.0 x 56.0 x 193.5 mm
HEL-04-01000-02
aluminum nut_pmm x 12
HEL-04-01010-01
socket head thin cap screw_din x 28

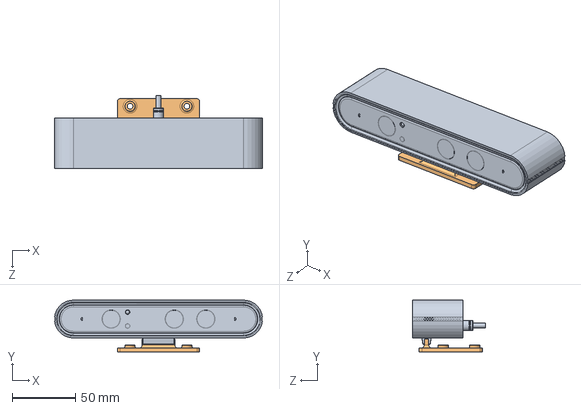
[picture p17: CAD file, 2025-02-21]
cad/solidworks 2023/HEL-03-01011-00.SLDASM
164.8 x 41.0 x 58.1 mm
HEL-06-01006-00
HEL-04-01013-02

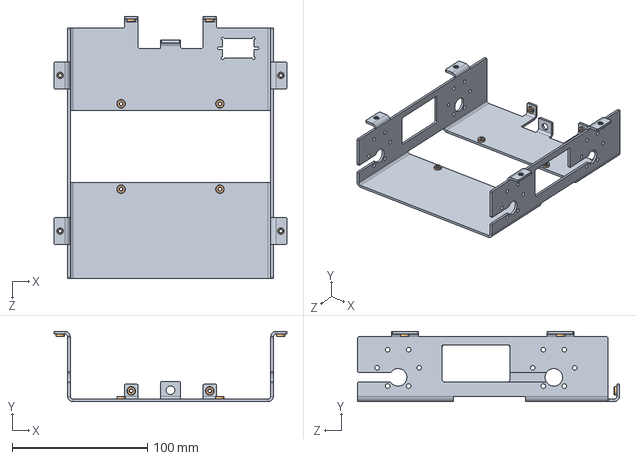
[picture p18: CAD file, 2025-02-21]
cad/solidworks 2023/HEL-03-01009-00.SLDASM
172.0 x 52.0 x 193.5 mm
HEL-04-01000-02
aluminum nut_pmm x 10

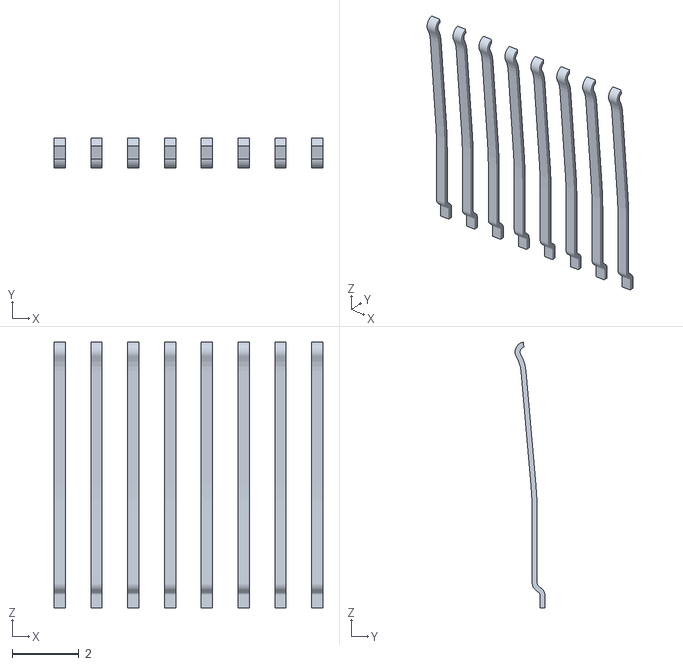
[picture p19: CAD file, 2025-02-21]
cad/stl/HEL-01-01000-02 - HEL-06-01011-00.STEP-1 RASPBERRY_PI_5_1.STEP_1.STEP-1 SLOT_CARD_ASM.STEP_1.STEP-1 CARD_SLOT_METAL_PIN.STEP_1.STEP-1.STL
8.04 x 0.892 x 7.95

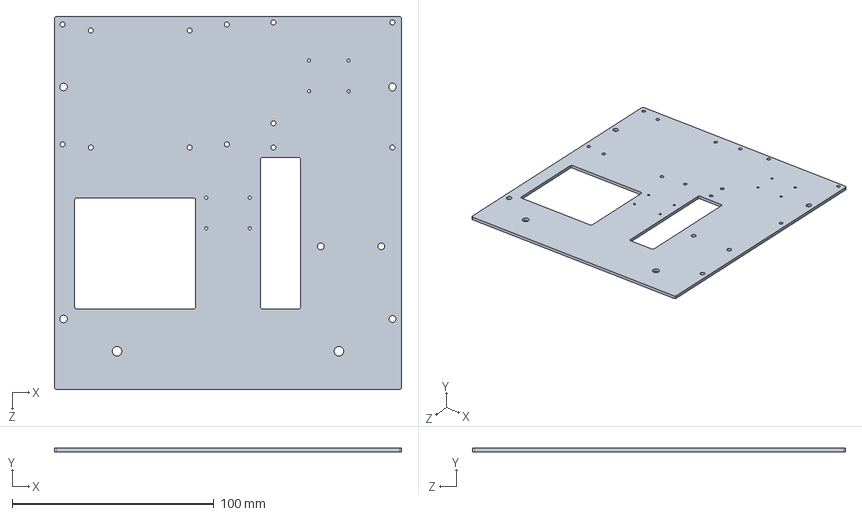
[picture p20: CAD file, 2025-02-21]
cad/solidworks 2023/HEL-04-01010-01.SLDPRT
172.0 x 2.00 x 185.0 mm

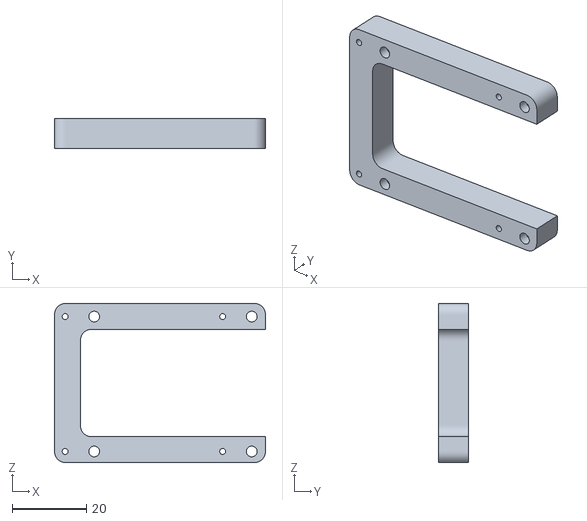
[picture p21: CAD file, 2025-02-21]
cad/stl/HEL-01-01000-02 - HEL-03-01006-00-1 HEL-04-01017-01-1.STL
57.0 x 8.00 x 43.0

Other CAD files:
cad/manufacturing_drawings/HEL-03-01010-00.STEP
cad/manufacturing_drawings/HEL-03-01009-00.STEP
cad/solidworks 2023/HEL-04-01009-01.SLDPRT
cad/stl/HEL-01-01000-02 - HEL-06-01011-00.STEP-1 RASPBERRY_PI_5_1.STEP_1.STEP-1 2.0_PIN_HEADER.STEP_1.STEP-1.STL
cad/manufacturing_drawings/HEL-03-01009-00.SLDDRW
cad/manufacturing_drawings/HEL-03-01010-00.SLDDRW
cad/solidworks 2023/HEL-04-01000-02.SLDPRT
cad/solidworks 2023/HEL-04-01004-00.SLDPRT
cad/solidworks 2023/HEL-04-01013-01.SLDPRT
cad/solidworks 2023/HEL-04-01013-02.SLDPRT
cad/solidworks 2023/HEL-04-01017-01.SLDPRT
cad/solidworks 2023/HEL-04-02001-00.SLDPRT
cad/solidworks 2023/HEL-04-03000-01.SLDPRT
cad/solidworks 2023/HEL-04-03001-00.SLDPRT
cad/solidworks 2023/HEL-04-03002-00.SLDPRT
cad/solidworks 2023/HEL-04-03003-00.SLDPRT
cad/solidworks 2023/HEL-04-03004-01.SLDPRT
cad/solidworks 2023/HEL-04-04000-00.SLDPRT
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

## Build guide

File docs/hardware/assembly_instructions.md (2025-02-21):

# Assembly Instructions

Do you have all the parts listed in the [Bill of Materials](../bill_of_materials) ready? Then let's get started! This guide works for both the HelMoRo ROS 1 variant equipped with a NVIDIA Jetson Nano or the ROS 2 variant equipped with a Raspberry Pi 5.

## Task 0: Get Ready

Make sure you have the following tools at hand before you start assembling. 

**Material**

- Electronic components
- Generative parts (3D printed and laser-cut parts)
- Sheet Metals
- Fasteners

**Tools**

- 2 mm hex-head key
- 2.5 mm hex-head key
- 8 mm hex-head socket
- 18 mm wrench 
- Flat-head screwdriver
- TR9 Torx screwdriver
- Soldering equipment

**Skills**

- Basic mechanical assembly skills
- Soldering (connecting cables)

**Time**

- The estimated assembly time is 70 minutes.

## Task 1: Wheel assembly

**Assembly Time**

5 minutes / wheel

**Tools needed**

- 2 mm hex-head key
- 2.5 mm hex-head key

### Step 1: Motor

**Required Parts:**

- 1x HEL-04-01000-02 / Frame Mount (For first wheel only)
- 1x HEL-06-01009-00  / Motor
- 6x DIN 7984 - M3 x 8 --- 4.5N / Screw M3x8

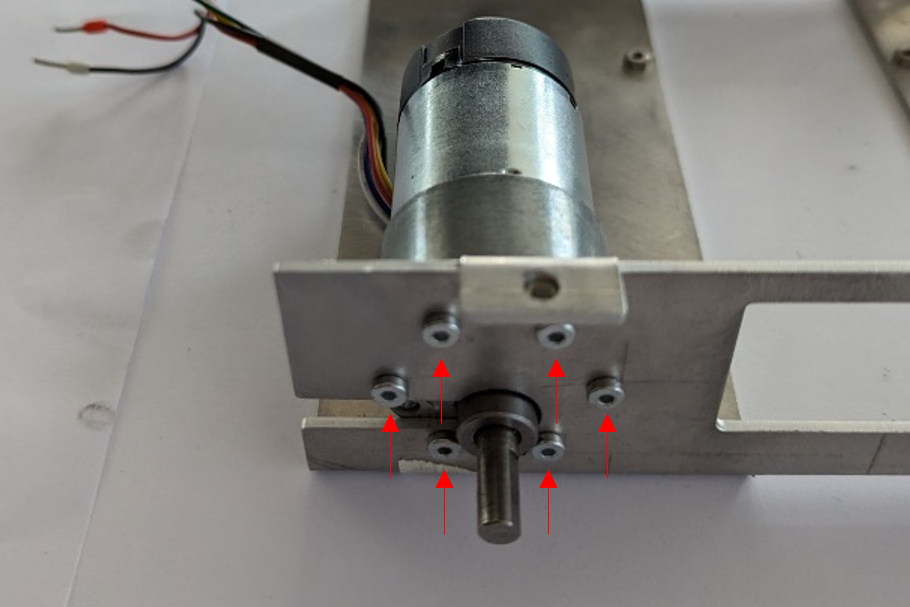
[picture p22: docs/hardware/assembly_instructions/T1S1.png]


Securely fix the motor into the frame mount using 6x M3x8 screws. The first motor should be attached where the frame mount does not allow for sliding in the motor (back right).

### Step 2: Wheel Adapter

**Required Parts:**

- 1x HEL-06-01002-00 / Wheel Adapter
- 1x DIN 7984 - M3 x 12 --- 10.5N / Screw M3x12 

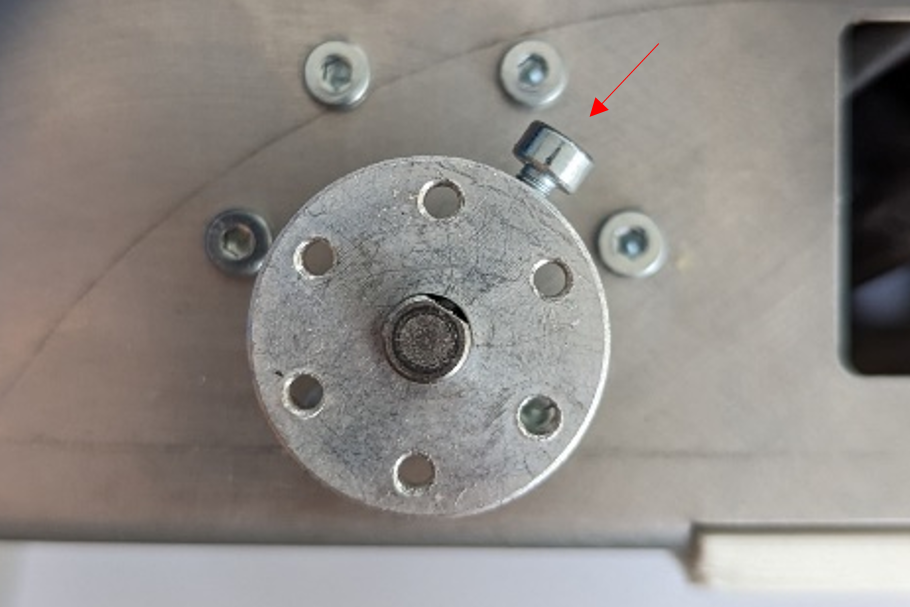
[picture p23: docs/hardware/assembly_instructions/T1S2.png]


Attach the wheel adapter to the motor assembly using 1x M3x12 screw.
Tighten the screw where the flange is flattened to stop it from rotating.

### Step 3: Wheel

**Required Parts:**

- 1x HEL-06-01000-00 / Wheel 
- 4x DIN 7984 - M3 x 8 --- 6.5N / Screw M3x8 

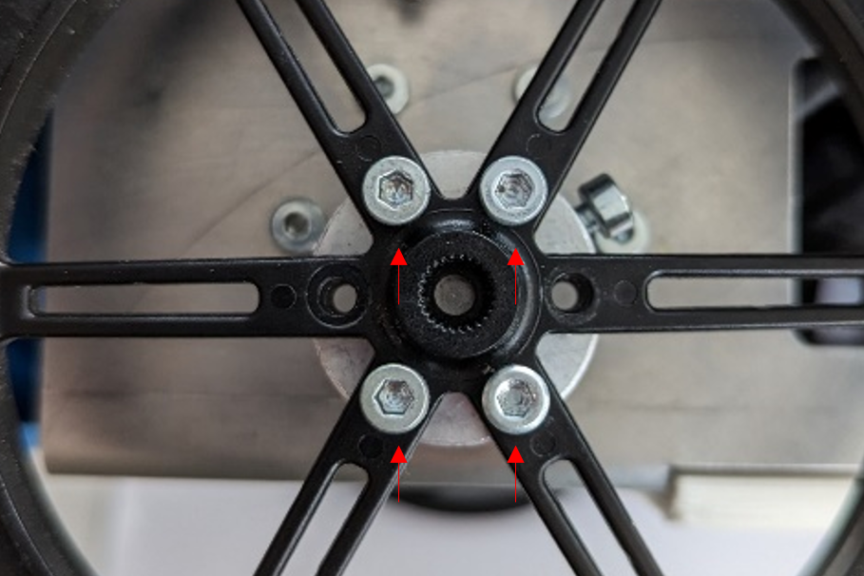
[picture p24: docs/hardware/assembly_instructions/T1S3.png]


Fix the wheel onto the wheel adapter using 4x M3x8 screws.

**Good job! Now 3 more to go.**

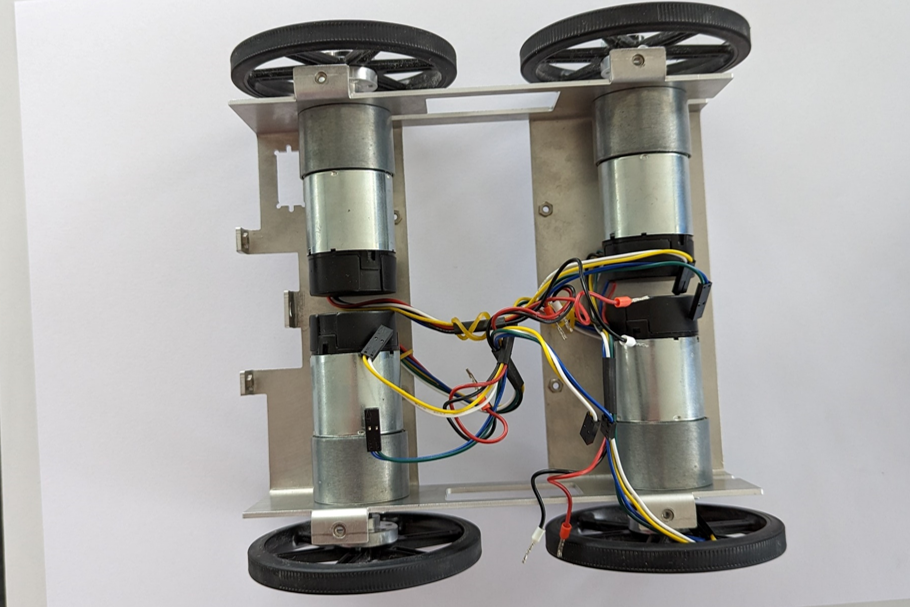
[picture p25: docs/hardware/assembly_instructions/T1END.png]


This is how the assembly should look after all the wheels have been attached.

## Task 2: Chassis

**Assembly Time**

30 minutes

**Tools needed**

- 2 mm hex-head key
- 2.5 mm hex-head key
- Flat-head screwdriver
- TR9 Torx screwdriver
- 8 mm hex-head socket

### Step 1: Motor Controller Plate

**Required Parts:**

- 1x HEL-04-01009-01 / Motor Controller Plate
- 1x HEL-04-01010-01 / Top Plate
- 2x ISO 4762 M3x4 / Screw M3x4

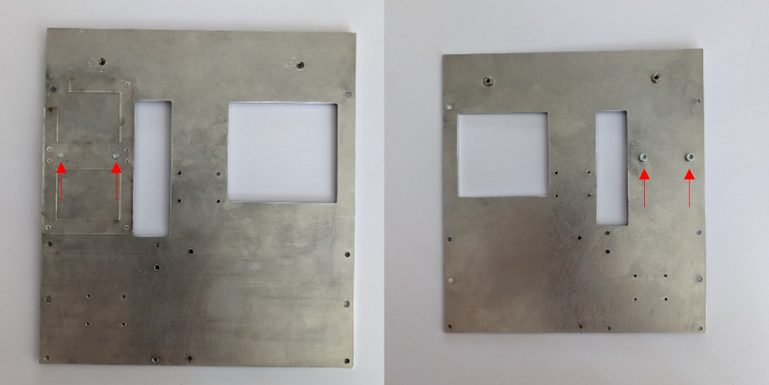
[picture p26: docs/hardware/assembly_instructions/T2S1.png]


Attach the motor controller plate to the top plate using 2x M3x4 screws.

### Step 2: IMU

**Required Parts:**

- 1x HEL-06-03003-00 / IMU
- 4x ISO 4762 M2 x 6 - 6N / Screw M2x6
- 4x Washer ISO 7092 – 2 / Washer M2

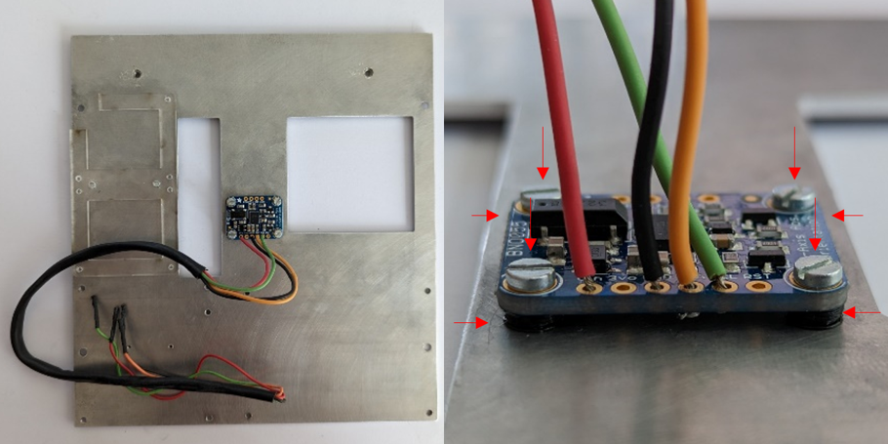
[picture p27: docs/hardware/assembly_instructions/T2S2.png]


Mount the IMU using 4x M2x6 screws and 4x M2 washers.

### Step 3: Top Plate on Frame Mount
**Required Parts:**

- 4x DIN 7984 - M3 x 8 --- 6.5N / Screw M3x8

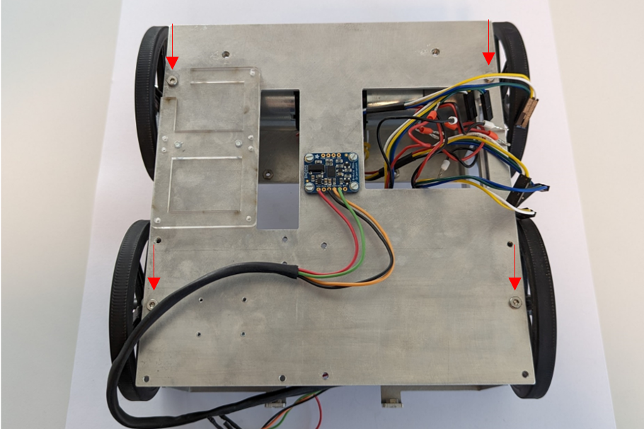
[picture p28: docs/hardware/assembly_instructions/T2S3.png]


Secure the top plate to the frame mount using 4x M3x8 screws.

### Step 4: Fan on Jetson (skip when using the Raspberry Pi)

**Required Parts:**

- 1x HEL-06-01005-00 / Fan
- 1x HEL-06-01003-00 / Jetson
- 4x ISO 14581 M2.5x16x16- / Screw M2.5x16
- 4x ISO - 4032 - M2.5 - D – N / Nut M2.5

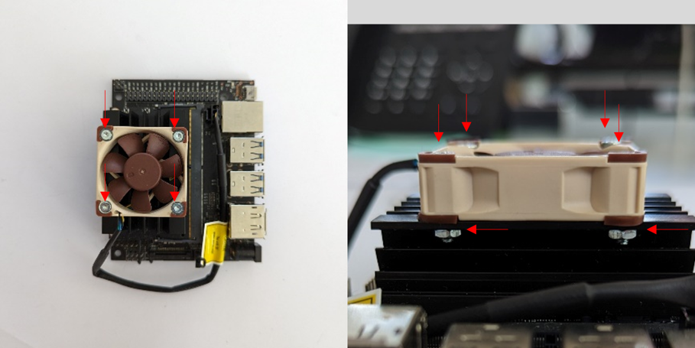
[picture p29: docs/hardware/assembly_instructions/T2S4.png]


In order to provide some cooling, install the fan on the Jetson using 4x M2.5x16 screws and 4x M2.5 nuts.

### Step 5: Mount Computer on Top Plate

**Required Parts:**

- 1x HEL-04-03004-00 / Base Plate
- 4x DIN 7984 - M3 x 8 --- 6.5N / Screw M3x8

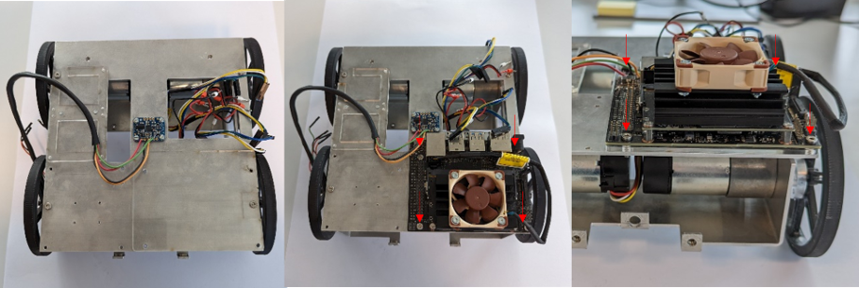
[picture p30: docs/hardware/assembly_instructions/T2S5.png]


Place the Base plate onto the Top Plate. Put the computer (Jetson Nano or Raspberry Pi 5) onto its base plate and attach both to the Top Plate using 4x M3x8 screws.

### Step 6: Mount Motor Controller

**Required Parts:**

- 2x HEL-06-01004-00 / Motor Controller Kit
- 8x Screw from Motor Controller Kit
- 1x HEL-04-01017-01 /  Holder Motorcontroller

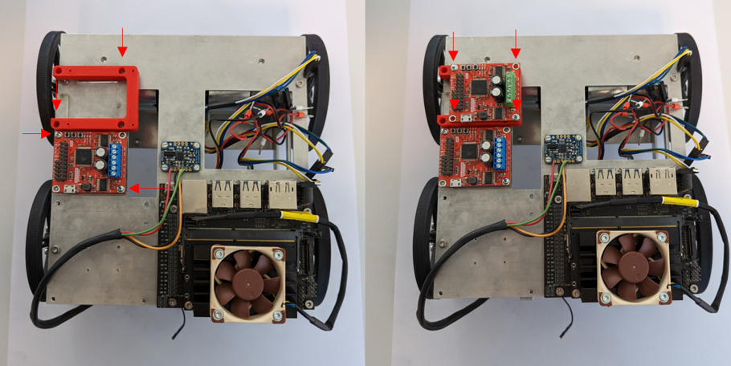
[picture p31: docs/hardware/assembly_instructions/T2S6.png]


Mount the first Motor Controller and the orange Motor Controller holder using the screws provided in the Motor Controller Kit. Attach the second Motor Controller on the Motor Controller Holder.

### Step 7: Connect Cables

**Required Parts:**

- 2x HEL-06-03005-00 / USB Cable

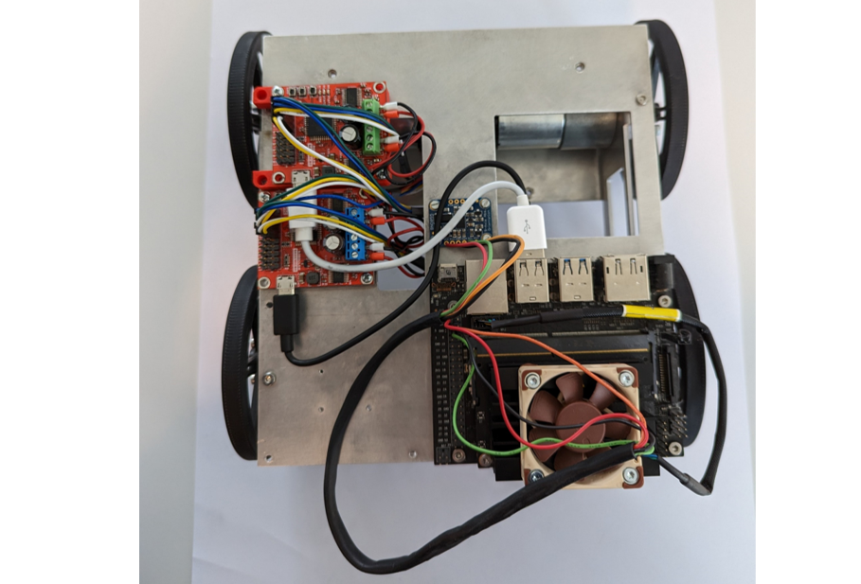
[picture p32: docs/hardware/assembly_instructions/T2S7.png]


Connect the USB cables as shown in the image and the [Electronic System Architecture](electronic_system_architecture.md). Make sure that the encoder is connected to the right motor.

### Step 8: Battery Protection

**Required Parts:**

- 1x HEL-06-04001-00 / Battery Protection 
- 1x Battery Connector (Deans M/F)
- 1x Battery Cable (EP Silicone Cable 0.5mm²)

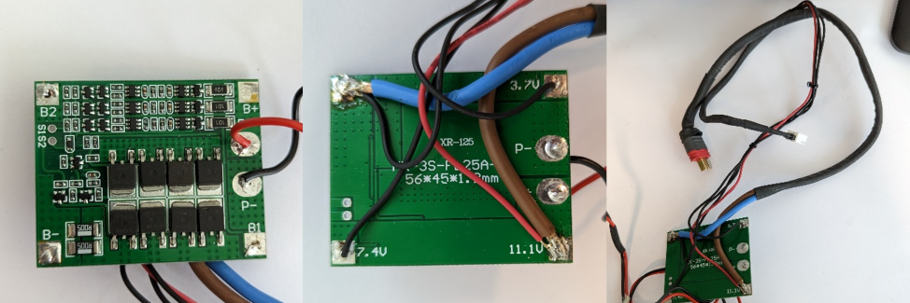
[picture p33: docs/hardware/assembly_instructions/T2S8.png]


Solder the Battery Cables and Battery Connector to the Battery Protection Module. Use the [Electronic System Architecture](electronic_system_architecture.md) as reference.

### Step 9: DC / DC Converter

**Required Parts:**

- 1x HEL-06-03004-00 / DC/DC Converter
- 1x HEL-06-04000-00 / Prototyping Board for DC/DC Converter
- 1x HEL-06-03001-01 / LED Voltmeter 
- 1x HEL-06-03002-00 / Power Switch

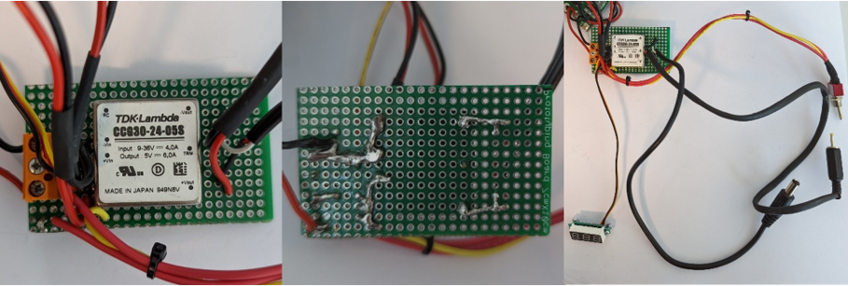
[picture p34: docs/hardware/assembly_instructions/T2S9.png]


Solder the connections of the DC/DC converter, LED Voltmeter, and Power Switch as shown in the image. The second image is mirrored so that you can compare it to the left image. Solder the connections according to the [Electronic System Architecture](electronic_system_architecture.md) and the Prototyping Board below.

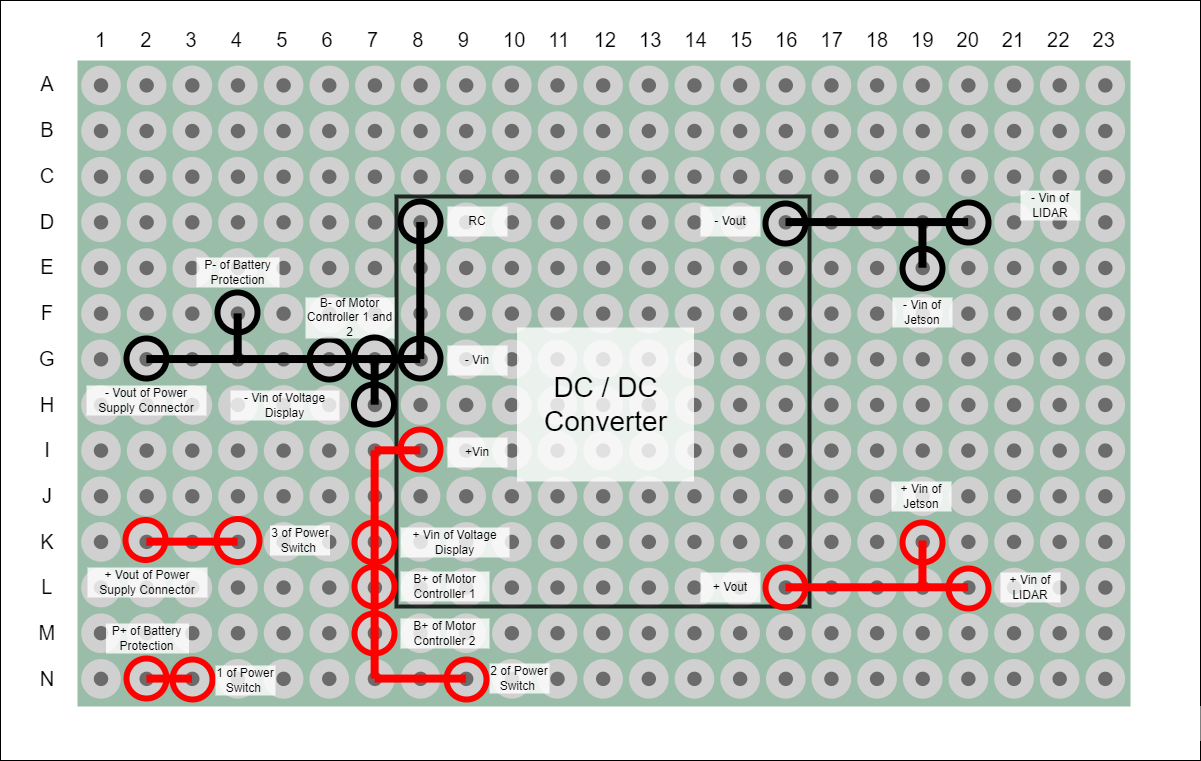
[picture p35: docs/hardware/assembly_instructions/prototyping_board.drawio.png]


### Step 10: Ciruit Board Box

**Required Parts:**

- HEL-04-04000-00 / Circuit Board Holder Base
- HEL-04-04001-00 / Circuit Board Holder Middle
- HEL-04-04002-00 / Circuit Board Holder Top
- 3x ISO 4762 M3 x 30 / Screw M3x30

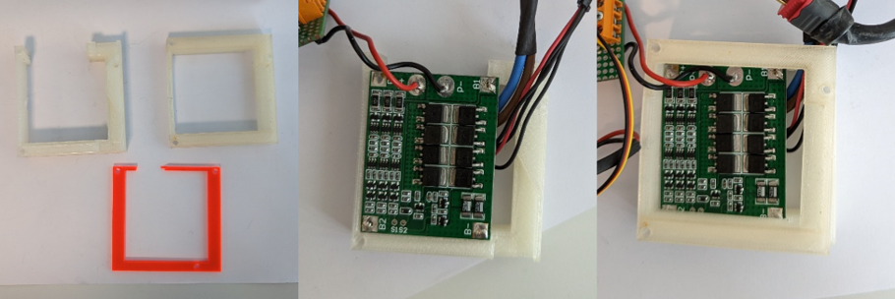
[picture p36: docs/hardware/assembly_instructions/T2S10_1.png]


Place the Battery Protection on the Circuit Board Holder Base. Make sure that the cables are oriented correctly so that they leave the box as shown in the image. Place the Circuit Board Holder Middle on the Battery Protection Module.

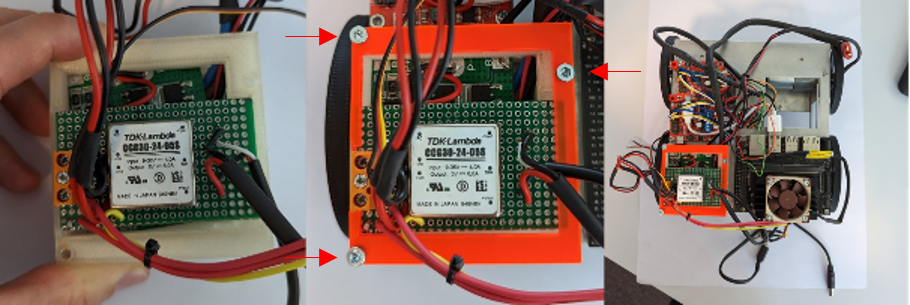
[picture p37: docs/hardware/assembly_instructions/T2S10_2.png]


Place the Prototyping Board with the DC/DC Converter on top of the Circuit Board Holder Middle . Assemble the whole Circuit Board Holder by using the Circuit Board Holder Top and 3x M3x30 screws.

### Step 11: Voltmeter

**Required Parts:**

- 2x DIN 7985A - M2x5 /  Screw M2x5
- 2x ISO - 4032 - M2 - D – N / Nut M2

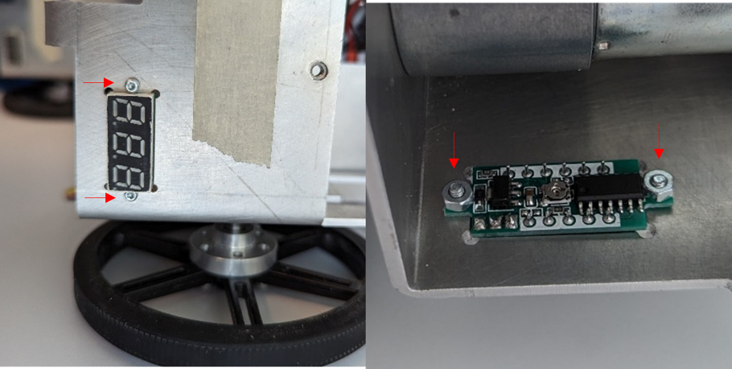
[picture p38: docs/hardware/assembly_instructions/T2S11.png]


Attach the voltmeter using 2x M2x5 screws and 2x M2 nuts.

### Step 12: Power Switch

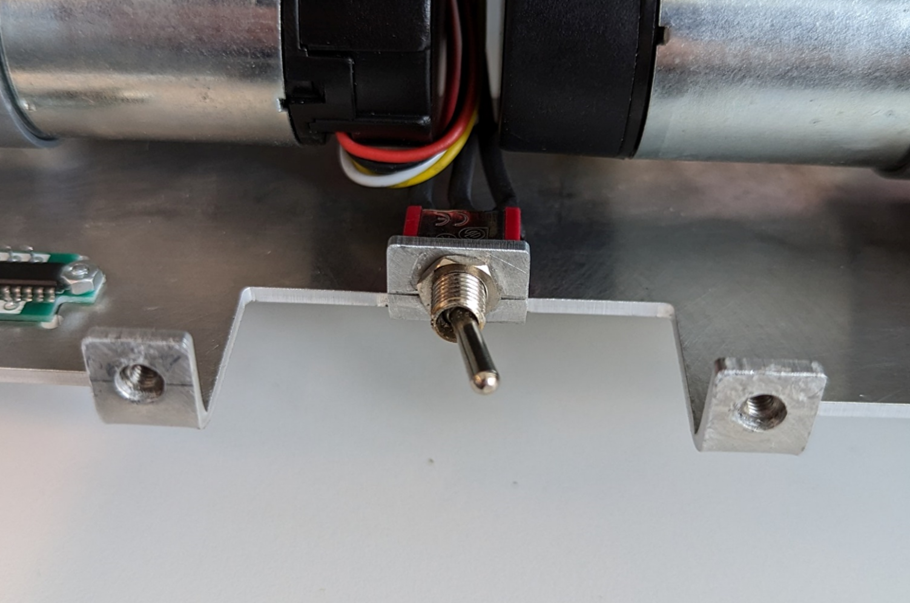
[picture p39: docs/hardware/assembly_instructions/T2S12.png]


Attach the Power Switch with the 8 mm hex-head socket.

### Step 13: Connect Cables

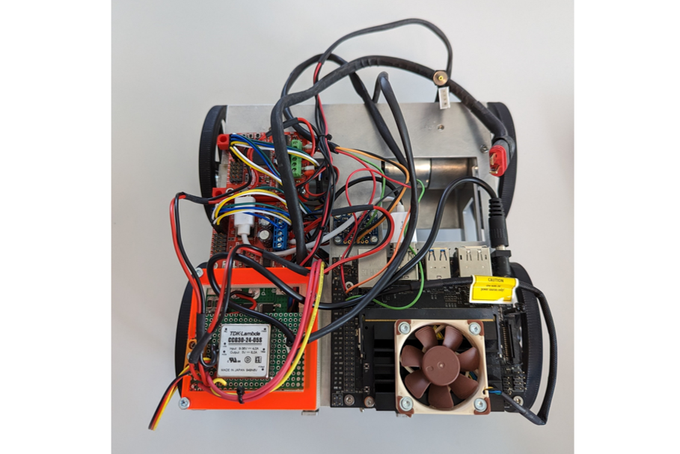
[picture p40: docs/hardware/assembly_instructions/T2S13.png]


Connect all the cables according to the [Electronic System Architecture](electronic_system_architecture.md). The cables to the battery and the one power cable to the LIDAR remain unconnected for now.

**Good job! Now lets continue with assembling the last part - the body.**

## Task 3: Body

**Assembly Time**

20 minutes 

**Tools needed**

- 2 mm hex-head key
- 2.5 mm hex-head key
- 18 mm wrench

### Step 1: Add Threaded Bushes to Body and Camera Plate

**Required Parts:**

- 1x HEL-04-03002-00 / Body
- 1x HEL-04-01013-02 / Camera Plate
- 12x Thread Insert MULTISERT 003M3 / Threaded Bush

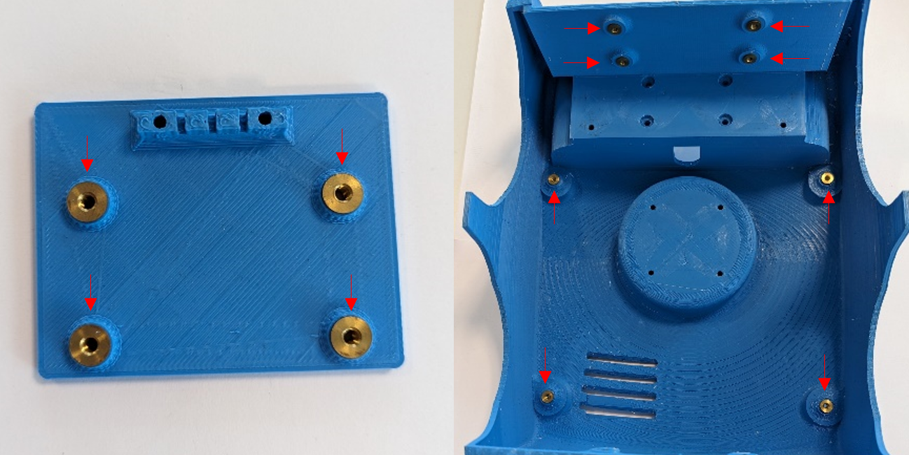
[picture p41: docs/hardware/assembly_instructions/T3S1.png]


Press the threaded bushes into the Body and Camera Plate while heating them with a soldering iron.

### Step 2: Power Supply Connector

**Required Parts:**

- 1x HEL-06-03000-00 / Power Supply Connector

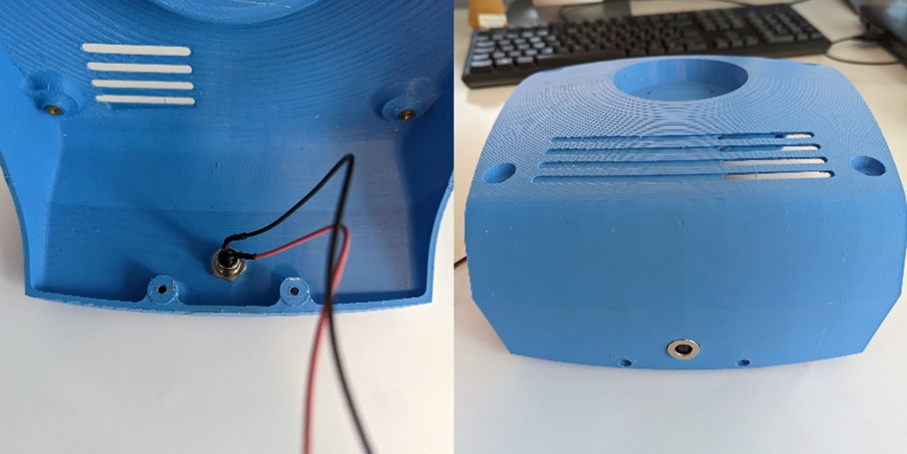
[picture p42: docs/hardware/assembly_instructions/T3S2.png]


Attach the Power Supply Connector to the robots body.

### Step 3: LIDAR

**Required Parts:**

- 1x HEL-06-01008-00 / LIDAR
- 1x HEL-06-01007-00 / LIDAR Adapter
- 4x DIN 7984 - M3 x 8 --- 6.5N / Screw M3x8

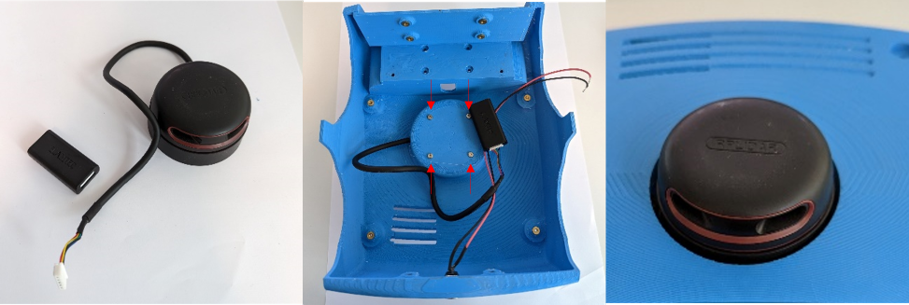
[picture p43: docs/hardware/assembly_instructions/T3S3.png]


Mount the LIDAR on the Body using 4x M3x8 screws.

### Step 4: Camera

**Required Parts:**

- 1x HEL-06-01006-00 / Camera
- 4x DIN 7984 - M3 x 8 --- 6.5N / Screw M3x8
- 2x DIN 7984 - M3 x 12 --- 10.5N / Screw M3x12

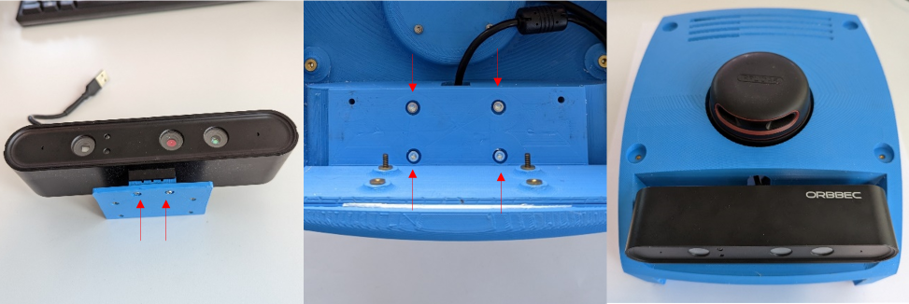
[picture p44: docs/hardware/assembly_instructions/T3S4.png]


Mount the Camera onto the Camera Plate with 2x M3x12 screws. Then attach the camera assembly to the robots body using 4x Threaded Bush and 4x M3x8 screws.

### Step 5: Merge Body and Chassis

**Required Parts:**

- 4x DIN 7984 - M3 x 18 / Screw M3x18

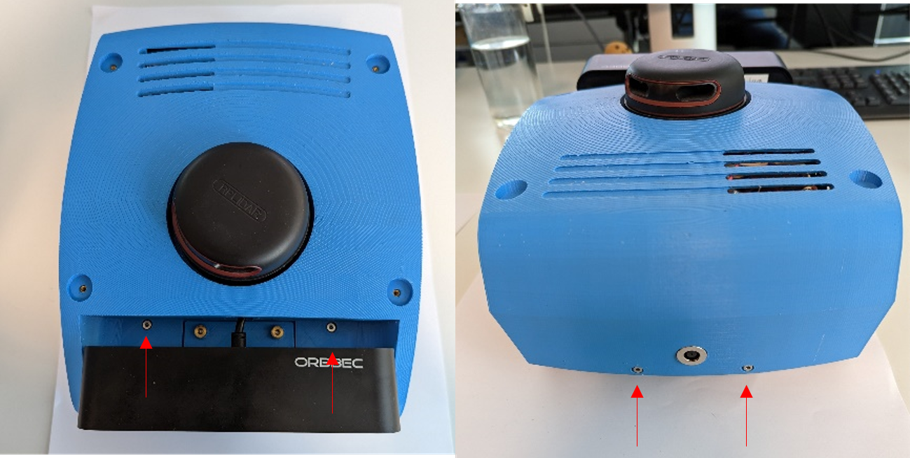
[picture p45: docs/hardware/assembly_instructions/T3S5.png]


Attach the body onto the chassis using 4x M3x18 screws.

### Step 6: Battery Holder

**Required Parts:**

- 1x HEL-04-01004-00 / Battery Holder
- 4x DIN 7984 - M3 x 8 --- 6.5N / Screw M3x8

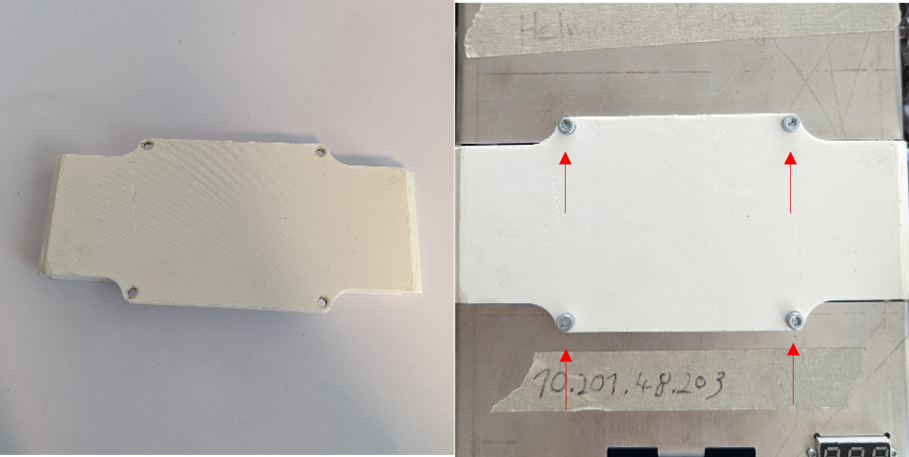
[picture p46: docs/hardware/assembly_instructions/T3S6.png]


Mount the Battery Holder on the bottom of the Frame Mount with 4x M3x8 screws.

### Step 7: Mount Front Part

**Required Parts:**

- 1x HEL-04-03003-00 / Front Part
- 2x ISO 4762 M3 x 30 / Screw M3x30

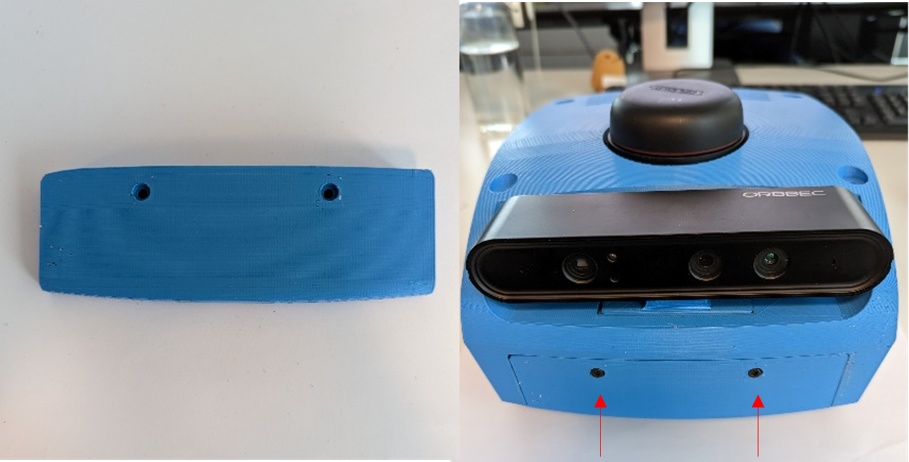
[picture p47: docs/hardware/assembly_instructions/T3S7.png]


Attach the Front Part to the Body with 2x M3x30 screws.

### Step 8: iPad Holder (optional)

**Required Parts:**

- 1x HEL-04-02001-00 / iPad Holder
- 4x ISO 4762 M3 x 40 / Screw M3x40

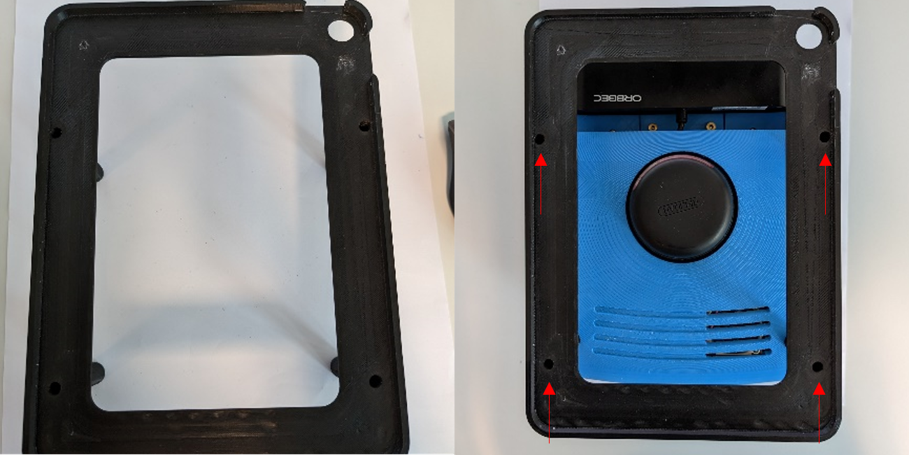
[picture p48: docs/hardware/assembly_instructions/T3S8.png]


Optionally, an iPad Holder can be attached to HelMoRo with 4x M3x40 screws.

### Step 9: Wheel Cap (optional)

**Required Parts:**

- 4x HEL-04-03000-01 / Wheel Cap

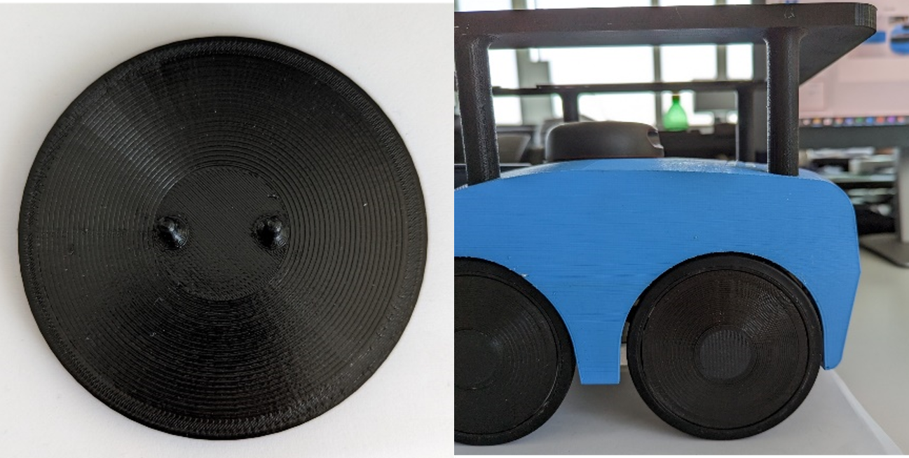
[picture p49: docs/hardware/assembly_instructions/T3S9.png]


Optionally, Wheel Caps can be attached to the wheel.

### Step 10: Fork (optional)

**Required Parts:**

- 1x HEL-04-03003-00 / Front Part with Fork
- 4x ISO 4762 M3 x 30 / Screw M3x30

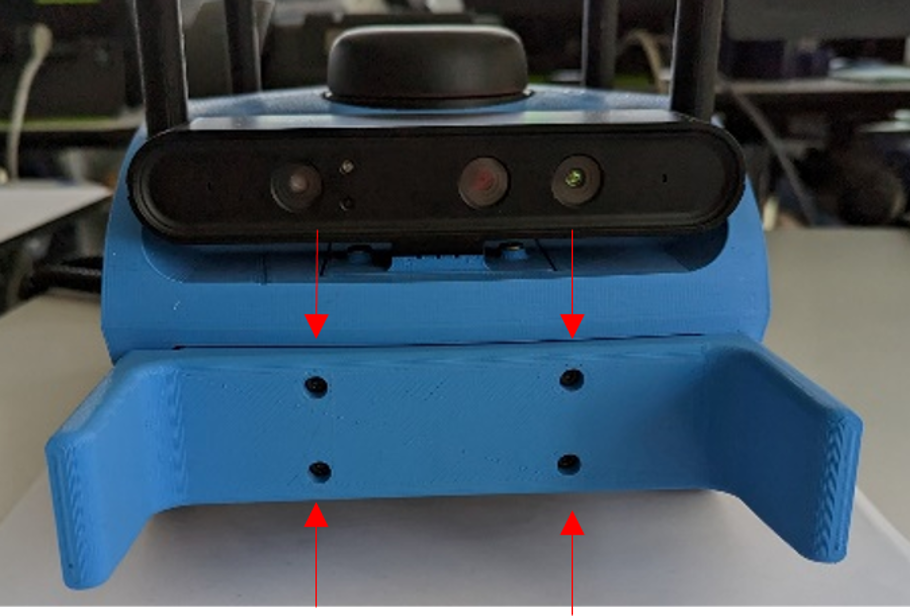
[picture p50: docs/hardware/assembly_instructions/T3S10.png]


Optionally, the front part can be replaced and a Fork can be added. The Fork can be attached by using 4x M3x30 screws.

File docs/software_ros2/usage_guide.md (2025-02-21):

# Usage Guide

When opening a new terminal always ensure that you sourced ROS. 
    ```sh
    source /opt/ros/humble/setup.bash
    ```

Alternatively you can also enable autonomous sourcing on terminal startup, by adding it to your .bashrc file.
    ```sh
    echo "source /opt/ros/humble/setup.bash" >> ~/.bashrc
    ```

Also always source your workspace when using a fresh terminal or after a change of any built pkgs.
    ```sh
    source ~/ros2_ws/install/setup.bash
    ```
## Start-Up
### Starting the simulation

1. Build the packages.
    ```sh
    cd ~/ros2_ws
    colcon build --symlink-install
    ```
2. Source the workspace.
    ```sh
    source install/local_setup.bash
    ```

3. Start the simulation.
    ```sh
    ros2 launch helmoro_sim_bringup helmoro_sim_launch.py
    ```

### Starting the Robot
1. SSH into the robot.
    ```sh
    ssh $(username of robot)@$(ip of robot)
    ```

2. Build the packages.
    ```sh
    cd ~/ros2_ws
    colcon build --symlink-install
    ```

3. Source the workspace.
    ```sh
    source install/local_setup.bash
    ```

4. Start the robot.
    ```sh
    ros2 launch helmoro_real_bringup helmoro_launch.py
    ```

5. For mapping visualization and camera streaming start RVIZ on the computer.
    ```sh
    ros2 launch helmoro_common_bringup rviz_launch.py
    ```

## Controlling the Robot
The robot can be controlled in multiple ways. The way we set it up, is to have operations packages within the folder helmoro_operation that use the topic /cmd_vel as an interface to control HelMoRo. In this example we created two packages. The joy control package and the navigation package. For controlling the robot with a joystick, use the joy control package. For autonomous navigation use the navigation package.

### Joy Control
In the simplest case one can drive Helmoro around using a joystick. In our case we used a Logitech joystick, which we connected to the laptop over Bluetooth. The left 'LT' and right triggers 'LT' accelerate and decellerate in x-direction respectively, and the left digital stick controls the rotation.

For this one needs to just start up either the [simulation](#starting-the-simulation) or the [robot](#starting-the-robot).

Before starting up the joystick make sure that the joystick is connected via the usb receiver to the computer. Also at the backside of the logitech controller you'll find a switch. Shift the switch to 'X' for XInput instead of 'D' for DirectInput such that floating point values will be broadcasted.
Also make sure to press the 'mode'-button such that the LED next to the 'mode'-button lights up. This is necessary for the correct mapping of the inputs. Secondly one needs to actually start the joystick node on the computer which is connected to the same network. Afterwards start the joystick manager.

``` sh
ros2 launch helmoro_joy_control joy_control.launch
```

Press the logitech button to wake up the controller, then press the 'LT' and 'RT' once to fully start the broadcasting of the velocity. To move forward use the 'RT' button while using the 'LT' Button to  move backwards. The left and right buttons on the left most (digital) joystick can be used to control the rotation.

### Autonomous Navigation
HelMoRo is able to navigate in a given space using the ROS Navigation Stack avoiding static and dynamic obstacles. Similarly HelMoRo can also navigate a unknown spaces avoiding static and dynamic obstacles while simulatinously mapping it by inluding the ROS SLAM stack too. In autonomous navigation mode it is possible to steer HelMoRo by sending PoseStamped msgs to the topic /goal_pose. In RVIZ this can be done by using the 2D Goal Pose functionality in the top bar.

image showing the goal pose button in the tobpbar of RVIZ Use the 2D Goal Pose to control HelMoRo

Autonomous navigation is included by default in the helmoro simulation and robot startup. If you want to use the navigation pkg without the robot, start it with.

```sh
ros2 launch helmoro_navigation nav_2.launch
```

More information can be found in the chapter [Autonomous Navigation using the Navigation Stack](#autonomous-Navigation-using-the-Navigation-Stack).

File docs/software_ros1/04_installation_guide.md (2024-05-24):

# Installation

The packages included in Helmoro support ROS Noetic on Ubuntu 20.04.

1. Install [ROS Noetic](http://wiki.ros.org/noetic/Installation) on Helmoros Nvidia Jetson and on your local machine.

2. Create a [ROS Workspace](http://wiki.ros.org/ROS/Tutorials/InstallingandConfiguringROSEnvironment)

      ```sh
      sudo apt install python3-catkin-tools
      mkdir -p ~/catkin_ws/src
      cd ~/catkin_ws/
      catkin build
      source devel/setup.bash
      ```
      
      Either you must run the above source command each time you open a new terminal window or add it to your .bashrc file as follows

      ```sh
      echo "source ~/catkin_ws/devel/setup.bash" >> ~/.bashrc
      ```

3. Clone the repository into your catkin workspace. The commands are stated in the following.

      ```sh
      cd ~/catkin_ws/src
      git clone https://github.com/Helbling-Technik/HelMoRo-software.git
      ```

After that, clone the required repositories and make the required installations listed in the next section [Dependencies](#dependencies).

## Dependencies

In the following, the packages and stacks which are required to run the Helmoro are mentioned. Do not forget to build the acquired packages once you cloned them into your workspace.

### Overview

- [catkin_simple](https://github.com/catkin/catkin_simple)
- any_node:
  - [message_logger](https://github.com/ANYbotics/message_logger)
  - [any_node](https://github.com/ANYbotics/any_node)
- [joystick_drivers stack](http://wiki.ros.org/joy)
- [helmoro_rplidar](https://github.com/Helbling-Technik/Helmoro_RPLidar)
- [ros_astra_camera_helmoro](https://github.com/Helbling-Technik/ros_astra_camera_helmoro)
- [ros_imu_bno055](https://github.com/dheera/ros-imu-bno055)
- [Navigation Stack](http://wiki.ros.org/navigation)
- [gmapping](http://wiki.ros.org/gmapping)
- [explore_lite](http://wiki.ros.org/explore_lite)

Clone or download all the required repositories or stacks all together with the following commands

```sh
sudo apt-get install ros-noetic-joy
cd ~/catkin_ws/src
git clone https://github.com/catkin/catkin_simple.git
git clone https://github.com/ANYbotics/message_logger.git
git clone https://github.com/ANYbotics/any_node.git
git clone https://github.com/Helbling-Technik/Helmoro_RPLidar
git clone --branch Helmoro_2.0 https://github.com/Helbling-Technik/ros_astra_camera_helmoro
sudo apt install ros-noetic-rgbd-launch
git clone https://github.com/dheera/ros-imu-bno055.git
sudo apt install ros-noetic-libuvc-camera ros-noetic-libuvc-ros ros-noetic-navigation ros-noetic-slam-gmapping
git clone https://github.com/hrnr/m-explore.git
cd ~/catkin_ws/
```

You should now be able to build all the installed packages with the followiung command

```sh
catkin build
```

In order to build and run the object_detector and the hand_detector, you will need to install additional OpenCV libraries. Please see [5.11 OpenCV](#opencv) for details.

### catkin_simple

catkin_simple is a package, that simplifies the task of writing CMakeLists.txt for a package. It is used in several packages and therefore required in order for them to be built properly using `catkin build`.

### any_node

any_node is a set of wrapper packages to handle multi-threaded ROS nodes. Clone or download the following repositories into your catkin workpace:

- [message_logger](https://github.com/ANYbotics/message_logger)

- [any_node](https://github.com/ANYbotics/any_node)

### joystic_drivers stack

This stack allows a joystick to communicate with ROS. Note that the Helmoro packages work exclusively with the Logitech Wireless joystick F710controller.
Additionally to the installation, it is useful to install the joystick testing and configuration tool

```sh
sudo apt-get install jstest-gtk
```

You can test the connection of your joystick by running `jstest-gtk` from terminal. Please check the device name (Helmoro packages use default joystick name "js0"). Also ensure that the mapping of the joystick is according to this screenshot:

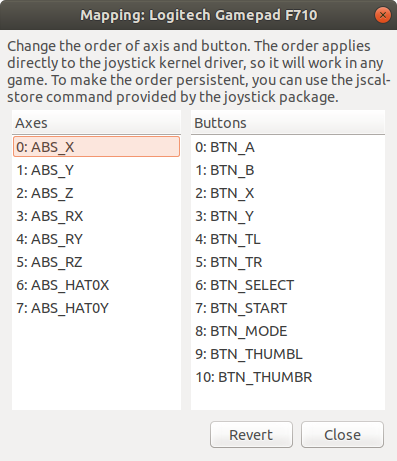
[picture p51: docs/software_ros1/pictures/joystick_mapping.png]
joystick_mapping


Ensure that you save the mapping for next time.

If your joystick has a different name eighter overwrite this value or pass your joystick name as an argument when launching the **helmoro.launch** file, which is explained in the following. To test the joystick functionality with ros run the following commands in two separate terminals:

```sh
roscore
```

```sh
rosrun joy joy_node
```

If you listen to the topic _/joy_ while using the joystick you should see the commands being published to the corresponding topic.

```sh
rostopic echo /joy
```

[joy roswiki](http://wiki.ros.org/joy)

### helmoro_rplidar

This package allows a [Slamtec RPLidar](https://www.slamtec.com/en/Lidar) to communicate with ROS. The repository has been derived from the official [rplidar_ros](https://github.com/slamtec/rplidar_ros). However, a small change in node.cpp had to be made for compatibility with the Helmoro and especially with the Navigation Stack.

The change that has been made can be found on line 61 of src/Node.cpp which now says:

```c++
scan_msg.header.stamp = ros::Time::now();
```

Instead of previously:

```c++
scan_msg.header.stamp = start;
```

Clone the [helmoro_rplidar](https://github.com/Helbling-Technik/Helmoro_RPLidar.git) repository into your workspace. This will create a package, still called rplidar_ros

Before you can run the rplidar, check the authority of its serial port.

```sh
ls -l /dev |grep ttyUSB
```

To add the authority to write to it:

```sh
sudo chmod 666 /dev/ttyUSB0
```

In order to fix the rplidar port and remap it to /dev/rplidar input the following command to your terminal

```sh
~/catkin_ws/src/rplidar_ros/scripts/create_udev_rules.sh
```

Once you have remapped the rplidar USB port, change the rplidar launch files about the serial_port value.

```xml
<param name="serial_port" type="string" value="/dev/rplidar">
```

You can run the rplidar as a standalone by typing the following command into your terminal:

```sh
roslaunch rplidar_ros rplidar.launch
```

For further information, head to:

- [rplidar roswiki](http://wiki.ros.org/rplidar)
- [rplidar Tutorial](https://github.com/slamtec/rplidar_ros)

### ros_astra_camera

This package allows a [Orbbec Astra](https://orbbec3d.com/product-astra-pro) RGB-D camera to communicate with ROS. Through it, images and pointclouds coming from the camera as well as transformations between the different frames are published as topics.

Clone the [ros_astra_camera_helmoro](https://github.com/Helbling-Technik/ros_astra_camera_helmoro.git) repository into your workspace, switch to the branch `Helmoro_2.0` and install its dependencies by entering the following command into your terminal and replace `ROS_DISTRO` by the ROS distribution you are currently using (in this case `melodic`):

```sh
sudo apt install ros-$ROS_DISTRO-rgbd-launch ros-$ROS_DISTRO-libuvc ros-$ROS_DISTRO-libuvc-camera ros-$ROS_DISTRO-libuvc-ros
```

You can run the astra camera as a standalone by typing the following command into your terminal:

```sh
roslaunch astra_camera astra.launch
```

We had to fork the normal [ros_astra_camera repository](https://github.com/orbbec/ros_astra_camera), as we needed to change some small values in the tf of the camera.

### ros_imu_bno055

This repository provides a node that lets the BNO055 IMU, which is built into Helmoro, publish its fused as well as its raw data over ROS via i2c.

Clone the [ros_imu_bno055](https://github.com/dheera/ros-imu-bno055) repository into your workspace.

In order to get the imu_bno055 package to work, first check if the IMU shows up in the i2c-ports.

```sh
ls -l /dev/i2c*
```

Furthermore, check you can run

```sh
sudo i2cdetect -y -r 1
```

You should be able to see your device at address 0x28, which is the default address of the IMU BNO055.

If everything works, you can run your IMU by simply launching:

```sh
roslaunch imu_bno055 imu.launch
```

### gmapping

Gmapping is a SLAM algorithm that can be used for the task of mapping an environment using a Lidar and the robot's odometry information.

Gmapping can be installed using the following command:

```sh
sudo apt-get install ros-melodic-slam-gmapping
```

For more details about SLAM gmapping, head to section [Slam using Gmapping](06_algorithms.md#slam-using-gmapping)

### Navigation Stack

The navigation stack allows Helmoro to navigate autonomously by using the sensor data of the rplidar, astra camera and odometry.

Install the navigation stack by typing the following command into your terminal:

```sh
sudo apt-get install ros-melodic-navigation
```

For more details about SLAM gmapping, head to section [Autonomous Navigation using the Navigation Stack](06_algorithms.md#autonomous-navigation-using-the-navigation-stack)

### explore_lite

In order to let Helmoro map its environment autonomously, you can make use of the explore_lite package.

Clone the [explore_lite](https://github.com/hrnr/m-explore) repository into your workspace.

For more details about explore_lite, head to section [Autonomous Slam using explore_lite](06_algorithms.md#autonomous-slam-using-explore_lite)

### OpenCV

#### Background

The Jetson Nano's default software repository contains a pre-compiled OpenCV 4.1 library (can be installed using `sudo apt install ...`).

The pre-compiled ROS tools all use OpenCV 3.2 (if ROS is installed using `sudo apt install ...`). If a custom ROS node uses OpenCV, it will use OpenCV 4.1 when being compiled, and is thus not compatible with other ROS tools/nodes (you might be lucky, but the object_detector uses incompatible OpenCV functions). It is thus required to install OpenCV 3.2 on the Jetson Nano, and since no pre-compiled library of OpenCV 3.2 for the Jetson Nano exists, this must be done from source.

Google's mediapipe uses OpenCV 4, and it is straightforward to compile the hand_detector node. However, GPU support is not enabled in the pre-compiled OpenCV 4.1 library. Hence, the OpenCV 4.1 library must also be installed from source if the hand_detector node should run on the GPU (recommended).

#### Installing OpenCV 3.2 or 4

1. Create a temporary directory, and switch to it:

   ```sh
   mkdir ~/opencv_build && cd ~/opencv_build`
   ```

2. Download the sources for OpenCV 3.2 or OpenCV 4 (any version > 4 should work) into `~/opencv_build`. You will need both `opencv` and `opencv_contrib` packages. The source files can be downloaded under the following links: [opencv](https://github.com/opencv/opencv/releases), [opencv_contrib](https://github.com/opencv/opencv_contrib/releases).
3. Make a temporary build directory and unzip the folders in your build directory. The folder structure should look like this:

      ```sh
      ~/opencv_build/
      ~/opencv_build/opencv/
      ~/opencv_build/opencv_contrib/
      ```

4. Create a build directory, and switch to it:

      ```sh
      cd ~/opencv_build/opencv
      mkdir build && cd build
      ```

5. Set up the OpenCV build with CMake. For a basic installation:

      ```sh
      cmake -D CMAKE_BUILD_TYPE=RELEASE \
      -D CMAKE_INSTALL_PREFIX=/usr/local \
      -D INSTALL_C_EXAMPLES=ON \
      -D INSTALL_PYTHON_EXAMPLES=ON \
      -D OPENCV_GENERATE_PKGCONFIG=ON \
      -D OPENCV_EXTRA_MODULES_PATH=~/opencv_build/opencv_contrib/modules \
      -D BUILD_EXAMPLES=ON ..
      ```

      To configure your OpenCV build more easily, install a CMake GUI, `sudo apt install cmake-qt-gui` or `sudo apt install cmake-curses-gui` and run it with `cmake-gui`.
      To run the hand_detector on GPU, which is based on Google's mediapipe, you need to configure your OpenCV build to support CUDA/GPU.

6. Start the compilation process:

      ```sh
      make -j8
      ```

      Modify the `-j` according to the number of cores of your processor. If you don't know the number of cores, type `nproc` in your terminal.

      The compilation will take a lot of time. Go grab a coffee and watch some classic [youtube videos](https://www.watson.ch/spass/youtube/278020811-die-21-besten-viralen-videos-der-schweiz).

7. To verify whether OpenCV has been installed successfully, type the following command.

      ```sh
      pkg-config --modversion opencv4
      ```

      (adjust the command for `opencv3`, `opencv2`, ...).

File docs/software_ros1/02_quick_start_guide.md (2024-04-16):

# Quick Start Guide

After setting up ROS and (in the best case) all needed repositories on your computer following the [Installation Guide](04_installation_guide.md) you can use Helmoro. Helmoro can be run in simulation using gazebo locally on your computer or as a real robot. If you require more information and tips read chapter [Detailed Usage](03_detailed_guide.md).

## Quick Setup

### Simulation

To run Helmoro in simulation just add the following flags:

```sh
is_real_robot:=false use_rviz:=true use_gui:=true
```

to the end of the roslaunch command shown in [Launching](#launching). This will start virtual Helmoro, RVIZ, Gazebo and the joystick reader on your local computer, e.g.

```sh
roslaunch helmoro_description nav_helmoro.launch is_real_robot:=false use_rviz:=true use_gui:=true
```

which should work out of the box, if you followed the Installation guide. The section [Launching](#launching) will provide you with further detail and different launch scripts.

### Real Robot

To run the physical Helmoro you will need to set up your own computer to communicate with Helmoro. For that you first need to find out Helmoro's IP address and connect it to the same wireless network as the computer.
Connecting Helmoro to the WiFi network is easiest done by plugging the Nvidia Jetson nano to an external monitor and connecting it to the wireless network using the ubuntu gui. As you will need to know its IP address later on it is convenient to assign it a static IP such that is stays constant within the network. This can be done via the router settings and is different for each router. The general idea is to link the Jetson mac address to some static IP.

Remember both `<Your_IP>` being the IP of your linux system and `<Helmoro_IP_address>` being the IP of Helmoro in your used network. More info under [Run](03_detailed_guide.md#run).

Now you will need to set environment variables on both devices. This is either done by typing the following commands in all terminals or by adding the following to your .bashrc and thus making it permanent per machine ('nano ~/.bashrc' and paste the lines below).

```sh
export ROS_IP=<Your_IP>
export ROS_MASTER_URI=http://<Helmoro_IP_address>:11311
```

The computer additionally needs the ROS_HOSTNAME in order to run the joystick manager.

``` sh
export ROS_HOSTNAME=<Your_IP>
```

To run commands on Helmoro you will need to ssh into the NVIDIA Jetson:

```sh
ssh <username>@<Helmoro_IP_address>
```

Where `<username>` will be "helmoro" if you followed the [Installation](04_installation_guide.md) and `<Helmoro_IP_address>` being the IP of Helmoro in your used network.

<!-- After executing the desired `launch file` (see below in [Launching](#launching)) you need to run

```sh
rosrun rviz rviz -d `rospack find helmoro_description`/rviz/rviz_config.rviz
```

on your computer for visualization RVIZ.

For remote control of velocity and the commanding of autonomous object pickup the joystick:

```sh
roslaunch helmoro_joymanager joymanager.launch
```
--->

## Launching

Run these commands on Helmoro or locally depending on your desired [Setup](#quick_setup).

### Joystick control

In the simplest case one can drive Helmoro around using the Logitech joystick. The left 'LT' and right triggers 'LT' are x-velocity and the left digital stick controls the rotation.

For this one needs to first start one of the many different launch files on Helmoro (by connecting via ssh) which also starts up the ROS Master. In the simplest case one starts the ```helmoro.launch``` which does not build a local obstacle map:

``` sh
roslaunch helmoro_description helmoro.launch
```

Secondly one needs to actually start the joystick node on the local ubuntu computer which is connected to the same network. Before doing so make sure the joystick is connected via the usb receiver to the computer.
Similarly, shift the switch to 'X' for XInput instead of 'D' for DirectInput such that floating point values will be broadcasted.
Also make sure to press the 'mode'-button such that the LED next to it lights up. This is necessary for the correct mapping of the inputs.

``` sh
roslaunch helmoro_joymanager joymanager.launch
```

Press the logitech button to wake up the controller, then press the 'LT' and 'RT' once to fully start the broadcasting of the velocity. To move forward use the 'RT' button while using the 'LT' Button to  move backwards. The left and right buttons on the left most (digital) joystick can be used to control the rotation.

### Autonomous Navigation to set goal positions

Helmoro is able to navigate in a given space using the ROS Navigation Stack avoiding static and dynamic obstacles along the calculated path. In this mode it is possible to send helmoro to goals using RVIZ and use every functionality from [joystick control](#joystick-control). You need to use Helmoro in a premapped environment. The premapped environment is set in the move ``move_base.launch`` file.
To run helmoro in new environment, first a map needs to be created with [Remote controlled mapping](#remote-controlled-mapping) or [Autonomous mapping](#autonomous-mapping)

Run the following on helmoro (connected via ssh) to launch the autonomous navigation:

```sh
roslaunch helmoro_description nav_helmoro.launch
```

Once ``nav_helmoro`` is launched one can run the following on the local machine:

``` sh
rosrun rviz rviz -d `rospack find helmoro_description`/rviz/rviz_config.rviz
```

This will start up Rviz and you can use the '2D Pose Estimate' and '2D Nav Goal' buttons to estimate its initial position and set its goal position on the map as in the image below. Make sure the checkmark for the occupancy map' is activated.

helmoro_intro

More information can be found in the chapter [Autonomous Navigation using the Navigation Stack](#autonomous-Navigation-using-the-Navigation-Stack).

### Object detection and autonomous pickup

In this mode Helmoro saves the location of objects, which he sees with his camera, in a map. The objects are displayed in RVIZ. Afterwards he can be commanded to bring the object back to a before specified location (`global goal` in `helmoro_navigation_goals/param/parameters.yaml`).  
After Helmoro detected the objects, the user can pick a color using the colored buttons on the [joystick](#joystick-control). Afterwards he can push start to command Helmoro to get the most often seen object. The back button cancels all autonomous actions from Helmoro.

```sh
roslaunch helmoro_description showcase_helmoro.launch
```

More information on the detection of object can be found in chapter [object_detector](#object_detector) and about the storage of the objects in a map in chapter [object map](#object_map).

### Remote controlled mapping

Helmoro can make use of a SLAM algorithm called gmapping, that uses the laser scans from the lidar and the odometry information coming from encoders and the IMU in order to build a map of obstacles.

```sh
roslaunch helmoro_description gmapping_helmoro.launch
```

For this to work, Helmoro can be remotely driven around by [joystick](#joystick-control) until the map is fully registered. You can follow the status in RVIZ, when looking at the `occupancy map`. When finished run in a separate terminal on Helmoro

```sh
rosrun map_server map_saver -f <location and name of your_map>
```

will save the map for later use (edit `move_base.launch` accordingly).

More detailed information can be found in [SLAM using gmapping](#slam-using-gmapping)

### Autonomous mapping

With the help of the `explore_lite` package Helmoro is able to map his environment by himself.

```sh
roslaunch helmoro_description explore_helmoro.launch
```

You can follow the status in RVIZ, when looking at the `occupancy map`. When finished run in a separate terminal on Helmoro

```sh
rosrun map_server map_saver -f <location and name of your_map>
```

will save the map for later use (edit `move_base.launch` accordingly).

More detailed information can be found in [Autonomous SLAM using explore_lite](#autonomous-SLAM-using-explore_lite)

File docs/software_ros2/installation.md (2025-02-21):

#
## Installation on the PC
1. Install [ROS Humble](https://docs.ros.org/en/humble/Installation.html)

2. Create a workspace and clone our repository. For better readability we created the workspace in this guide within the home directory and named the workspace ros2_ws. But feel free to choose another directory and workspace name.

    ```sh
    mkdir ~/ros2_ws/src
    cd ~ros2_ws/src
    git clone https://github.com/Helbling-Technik/HelMoRo-software-ROS2.git
    ```

3. Install dependencies

    ```sh
    cd ~/ros2_ws
    sudo apt-get update
    rosdep install --from-path src -yi
    ```

4. Source ROS and build the HelMoRo software package

    ```sh
    source /opt/ros/humble/setup.bash
    cd ~/ros2_ws
    colcon build --symlink-install
    ```

5. Your folder structure should now look like this
    ```sh
    ~/ros2_ws
    ├── build
    ├── install
    ├── log
    └── src
        └── HelMoRo-software-ROS2
    ```

## Installation on the robot
1. Install [ROS Humble](https://docs.ros.org/en/humble/How-To-Guides/Installing-on-Raspberry-Pi.html)

2. Create a workspace and clone our repository. For better readability we created the workspace in this guide within the home directory and named the workspace ros2_ws. But feel free to choose another directory and workspace name.

    ```sh
    mkdir ~/ros2_ws/src
    cd ~ros2_ws/src
    git clone https://github.com/Helbling-Technik/HelMoRo-software-ROS2.git
    ```

3. Clone the repo for communication with the lidar, IMU and camera

    ```sh
    git clone https://github.com/flynneva/bno055.git
    git clone -b ros2 https://github.com/Slamtec/rplidar_ros.git
    git clone https://github.com/Helbling-Technik/HelMoRo_OrbbecSDK_ROS2.git
    ```

4. Install dependencies

    ```sh
    cd ~/ros2_ws
    sudo apt-get update
    rosdep install --from-path src -yi
    ```

5. Your folder structure should now look like this
    ```sh
    ~/ros2_ws
    ├── build
    ├── install
    ├── log
    └── src
        ├── bno055
        ├── HelMoRo_OrbbecSDK_ROS2
        ├── HelMoRo-software-ROS2
        └── rplidar_ros
    ```

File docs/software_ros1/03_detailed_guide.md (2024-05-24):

# Detailed Usage

In the following, it is explained how to use the Helmoro ROS architecture. Under `helmoro_description/launch/` you will find several launch files:

- helmoro.launch: Default launch file for Helmoro
- gmapping_helmoro.launch: Used for [gmapping](#slam-using-gmapping)
- nav_helmoro.launch: Used for the [Navigation Stack](#autonomous-navigation-using-the-navigation-stack)
- explore_helmoro.launch: Used for [explore_lite](#autonomous-slam-using-explore_lite)
- showcase_helmoro.launch: Used for the [showcase](#showcase)

In the following, only the usage on the main launch file, **helmoro.launch**, on which all other launch files depend on, is explained. However using the other launch files works analogously. Head to the linked sections to discover more about the purpose and usage of the other launch files.

## Run  

The main launch file to run all the required nodes of the Helmoro ROS architecture is **helmoro.launch** in the package **helmoro_description**.

In order to run Helmoro form a remote PC, you can use ssh as described in the following command.

```sh
ssh <username>@<IP-address>
```

Thereby, type in the username and instead of "IP" type in the IP-address of your Helmoro. Using this command, you can remotely log into the terminal of the Helmoro SBC and thus launch helmoro.launch from your remote device.

Once connected to helmoro via ssh, run the launch file with the following commands:

```sh
roslaunch helmoro_description helmoro.launch
```

### Running ROS across Multiple Machines

In some cases, you want to run ROS across multiple machines for example to visualize the published data of Helmoro externally on RViZ. To do so, you can open up two windows in the terminal of one of your machines and connect one of your terminals via ssh to the other machine. Select one machine to run your master on. In our case, this would be the Helmoro. This is where you would start your roscore or a launch file such as helmoro.launch.

A common problem, that occurs is that the machines cannot resolve each others hostname into an IP-address. Check if the IP-address of each machine is visible by typing:

```sh
echo $ROS_IP
```

If there is no IP-address showing up, you can set ROS_IP in each machine environment before starting a node by typing:

```sh
export $<Your_IP>
```

You can also use the following script in each terminal, after you filled in the required values

```sh
#!/bin/bash

source /opt/ros/noetic/setup.bash

# select workspace
source /home/$USER/<Your catkin workspace>/devel/setup.bash

# set IP of localhost, ethernet or wifi for using remote roscore
ip_temp=$(hostname -I)
#my_ip = localhost
my_ip=${ip_temp% }

# set IP of roscore
roscore_ip=$my_ip

export ROS_IP=$my_ip
export ROS_HOSTNAME=$my_ip
export ROS_MASTER_URI=http://$roscore_ip:11311

```

Then, enter the following commands in both terminals:

```sh
export ROS_MASTER_URI=http://<IP_of_Master>:11311
```

Thereby, type in the IP-address of your master-machine instead of <IP_of_Master>.

For further testing, you can use the [rostopic](http://wiki.ros.org/rostopic) tool on all machines that are connected to the master. Using the command
`rostopic list` you should get a list of all available topics. In wireless networks, which our Helmoro uses, it is sometimes necessary to check if there is a connection and messages still come.
You can do so by echoing a published topic.

```sh
rostopic echo /topic_name
```

If you are in the HTKZ lab network you can look for Helmoro's IP [here](http://intranet/grpit/DHCP_HTKZ-Labor.asp)

For further reference head to [ROS MultipleMachines](http://wiki.ros.org/ROS/Tutorials/MultipleMachines) and [ROS NetworkSetup](http://wiki.ros.org/ROS/NetworkSetup).

### Run RViZ with a config file

In order to run RViZ as a standalone directly with the custom config file, type in:

```sh
rosrun rviz rviz -d `rospack find helmoro_description`/rviz/rviz_config.rviz
```

## Arguments

You can pass several arguments to the **helmoro.launch** and other launch files, when running it using:

```sh
roslaunch helmoro_description helmoro.launch arg_name:=value
```

### Usage Arguments

The most important arguments for usage are depicted in the following table.

| Parameter | Default | Definition |
| --- | --- | --- |
| is_real_robot | true | Switch to use real robot or gazebo simulation |
| use_rviz | false | Switch to use rviz for visualization also activates the joystick |
| use_joystick | = use_rviz | Switch to use joystick |
| use_lidar | true | Switch to use lidar |
| use_rgbd_camera | true | Switch to use rgbd camera |

### RVIZ Arguments

| Parameter | Default | Definition |
| --- | --- | --- |
| rviz_config_file | rviz_config.rviz | Default rviz config file |

### Gazebo Arguments

| Parameter | Default | Definition |
| --- | --- | --- |
| paused | false | Switch if gazebo is started running or in paused mode |
| use_sim_time | true | Switch if simulated gazebo time or real time is used for simulation |
| gui | false | Switch if gui of gazebo is displayed |
| world | helmoro_gazebo_plugin/worlds/helmoro_wohnung_mob | Default testing world that is loaded for gazebo simulation |

### Common commands

To run Helmoro in simulation (in Gazebo) you can call this command on your local computer:

```sh
roslaunch helmoro_description showcase_helmoro.launch is_real_robot:=false use_rviz:=true use_gui:=true
```

You then can add a box into the environment and let Helmoro pick it up. Be reminded that in simulation helmoro does not have a fork (but he can push around objects) and that the odometry is better then in reality.

To run the required nodes for the showcase on Helmoro you can run:

```sh
roslaunch helmoro_description showcase_helmoro.launch
```

Additionally, the above written command to call rviz on your local computer

```sh
rosrun rviz rviz -d `rospack find helmoro_description`/rviz/rviz_config.rviz
```

You then also need to start the joystick node (on your computer) with:

```sh
 roslaunch helmoro_joymanager joymanager.launch
```

Make sure to connect the joystick to your computer

#### Advanced usage or tuning

If you want to tune the parameters of amcl or the navigation stack, while Helmoro is running you can open the dynamic reconfigure plugin after running:

```sh
rosrun rqt_gui rqt_gui
```

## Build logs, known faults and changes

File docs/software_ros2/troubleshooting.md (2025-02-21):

## Network 
In case you can't receive or send messages over your network, go through these checks:

1. Do your robot and computer have the same [ROS_DOMAIN_ID](https://docs.ros.org/en/foxy/Concepts/About-Domain-ID.html)?
2. Does your firewall block communication? Maybe you need to open ports?
    ```sh
    sudo ufw allow in proto udp to 224.0.0.0/4
    sudo ufw allow in proto udp from 224.0.0.0/4
    ```
3. Is multicasting enabled in your network interfaces? Is multicasting enabled in your router? Check by using the [multicast](https://index.ros.org/p/ros2multicast/) package.

## Motors

In case you are getting errors from the helmoro_motor_controls and the Roboclaw Motor Controllers are not working, go through the following quick checks:

1. Check if the port name of both Roboclaws appear when plugin in, the USB by typing `ls /dev/ttyACM*`
2. Check if you have the authority to write to this port. Otherwise type `chmod 666 <portname>` in order to add the authority.
3. Also, when connecting the motors with two USB cables, it can happen that the portnames of the left and the right roboclaw motor controller swap (`/dev/ttyACM0` <-> `/dev/ttyACM1`). Since, to this point their USB ports are not fixed. If this happens, simply swap the two addresses for the left and the right controller specified in the param file.

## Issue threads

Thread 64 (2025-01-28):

Update CAD of Website

mbloechli, 2025-01-28:
- Add Raspberry Pi to Assembly, give it a part number
- Add Raspberry plate to Assembly, give it a part number
- Create new iteration of top plate with holes for both Pi and Jetson
- Create a new iteration of full Assembly with Raspberry Pi, Pi plate and Top Plate

Closed 2025-01-29.

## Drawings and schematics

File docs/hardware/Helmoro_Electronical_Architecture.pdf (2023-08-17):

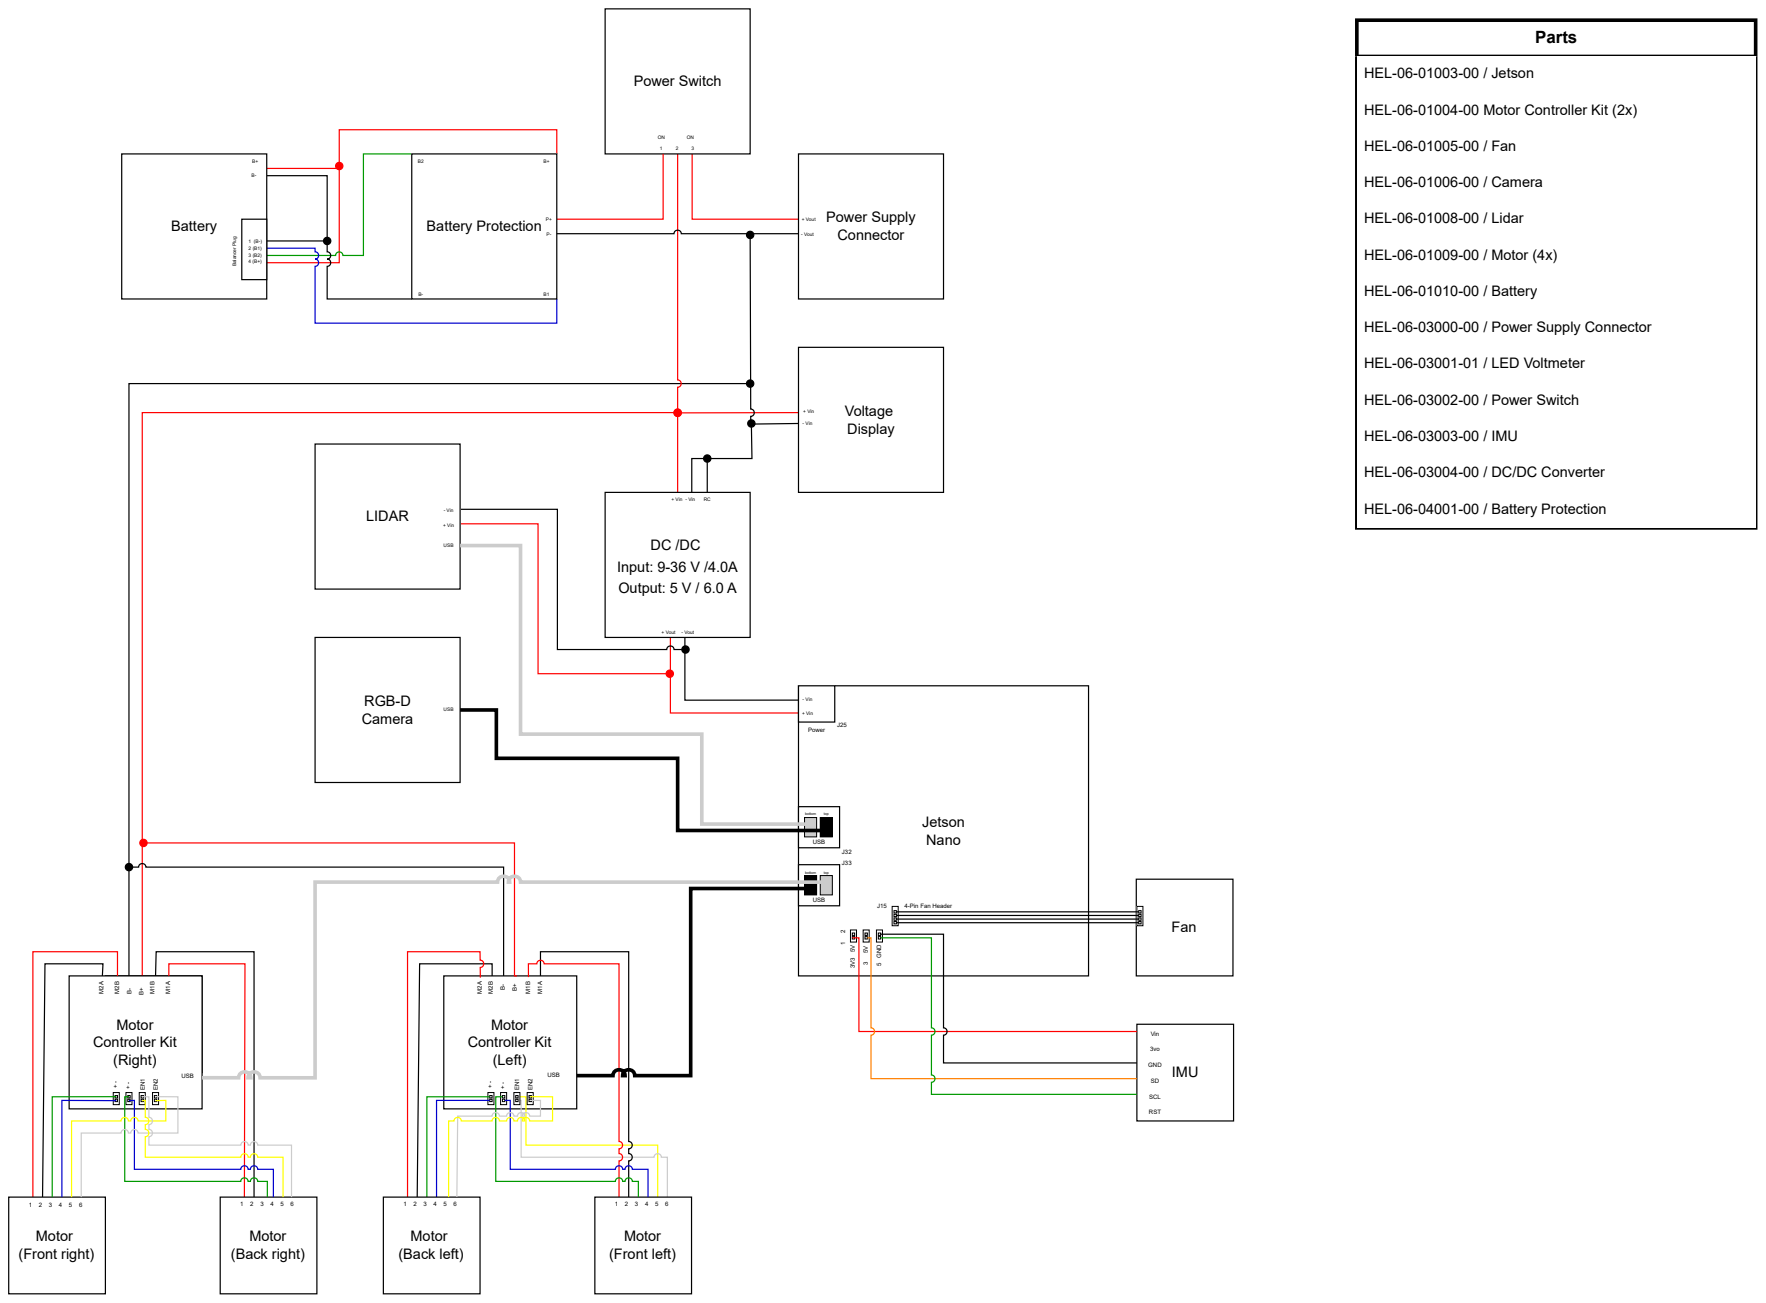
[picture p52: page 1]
Motor Controller Kit (Left); Motor driver 1 Motor; Motor (Front right); Power Switch; Voltage Display; DC /DC Input: 9-36 V /4.0A Output: 5 V / 6.0 A; Motor (Back right); RGB-D Camera; LIDAR; USB; Motor (Front left); Battery; Battery Protection; Balancer Plug; Power Supply Connector; Fan; Jetson Nano; bottom; top; Power; 5 GND; + Vin; - Vin; IMU; RST; Vin; GND; SCL; + Vin - Vin; + Vout; - Vout; Motor (Back left); Parts; HEL-06-01003-00 / Jetson; HEL-06-01005-00 / Fan; HEL-06-01006-00 / Camera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

HEL-06-01004-00 Motor Controller Kit (2x)

HEL-06-03000-00 / Power Supply Connector

HEL-06-03001-01 / LED Voltmeter

HEL-06-03002-00 / Power Switch

HEL-06-03004-00 / DC/DC Converter

HEL-06-04001-00 / Battery Protection

4-Pin Fan Header

Controller Kit | (Right)

USB

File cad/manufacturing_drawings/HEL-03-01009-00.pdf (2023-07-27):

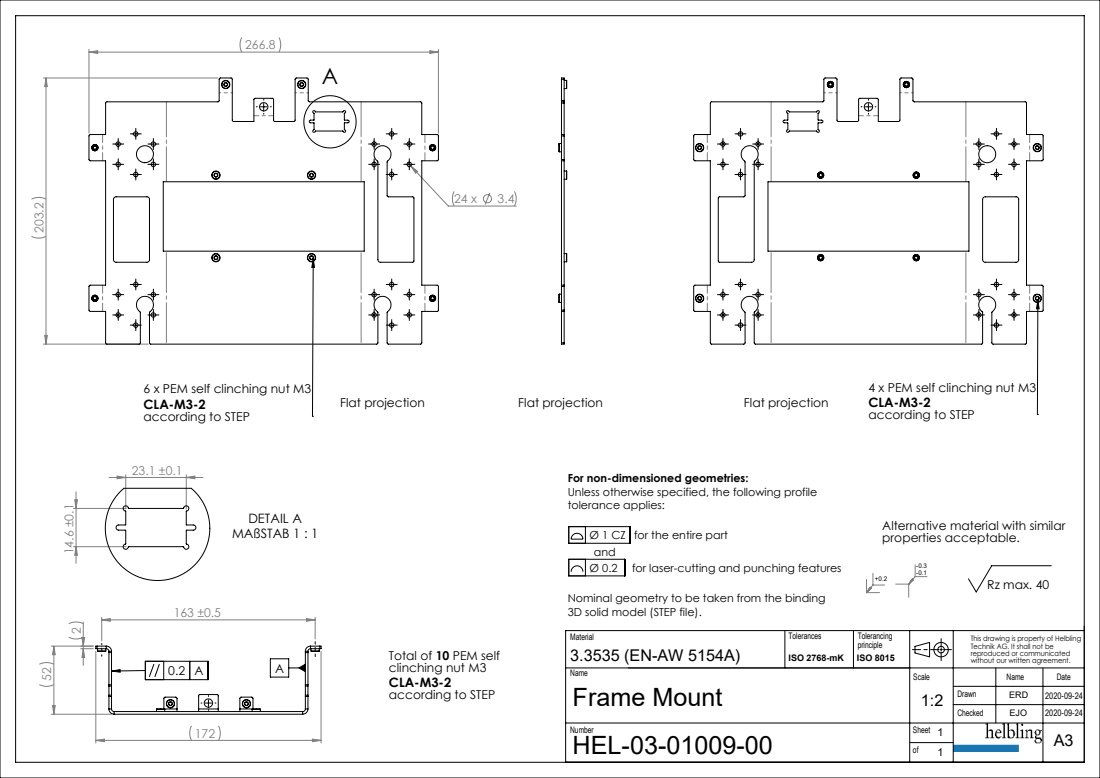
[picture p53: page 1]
DETAIL A MAßSTAB 1 : 1; Rz max. 40; for the entire part; for laser-cutting and punching features; Flat projection

6 x PEM self clinching nut M3
CLA-M3-2
according to STEP

4 x PEM self clinching nut M3

For non-dimensioned geometries:
Unless otherwise specified, the following profile
tolerance applies:

Alternative material with similar
properties acceptable.

Nominal geometry to be taken from the binding
3D solid model (STEP file).

Material Tolerances Tolerancing principle 3.3535 (EN-AW 5154A) ISO 2768-mK ISO 8015 | | This drawing is property of Helbling Technik AG. It shall not be reproduced or communicated without our written agreement.

Total of 10 PEM self
clinching nut M3

Name Frame Mount | Scale 1:2 | Name Date Drawn ERD 2020-09-24 Checked EJO 2020-09-24

Number HEL-03-01009-00 | Sheet 1 of 1 | | A3

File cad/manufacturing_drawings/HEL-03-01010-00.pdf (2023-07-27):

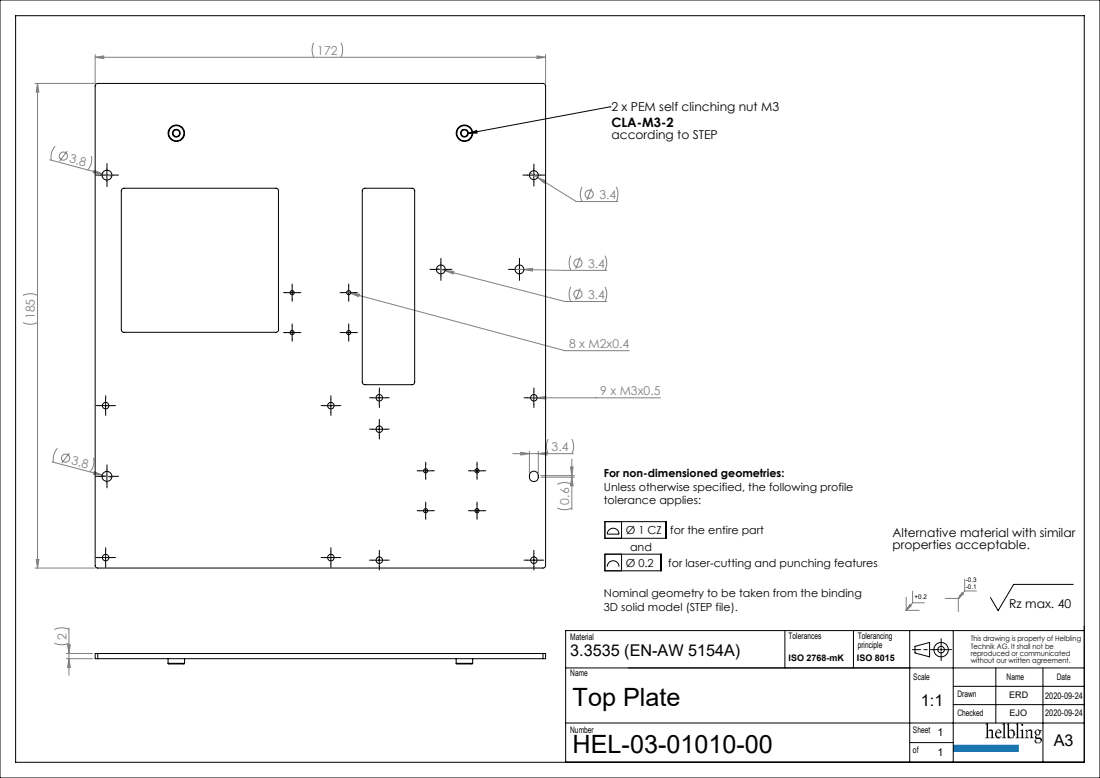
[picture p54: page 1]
Rz max. 40; for the entire part; for laser-cutting and punching features

2 x PEM self clinching nut M3
CLA-M3-2
according to STEP

For non-dimensioned geometries:
Unless otherwise specified, the following profile
tolerance applies:

Alternative material with similar
properties acceptable.

Nominal geometry to be taken from the binding
3D solid model (STEP file).

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

Name Top Plate | Scale 1:1 | Name Date Drawn ERD 2020-09-24 Checked EJO 2020-09-24

Number HEL-03-01010-00 | Sheet 1 of 1 | | A3

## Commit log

2023-06-05 added partial BOM and electronical architecture
    [Helmoro_2_BoM_28-03-2023.xlsx]
2023-06-05 refactored sections
    [Helmoro_2_BoM_28-03-2023.xlsx]
2023-06-05 completed BOM
2023-06-26 inserted asssembly instructions and updated BoM
2023-07-07 prototyping board
2023-07-07 auto import excel to md table
    [Helmoro_2_BoM_English­­_26-06-2023 - Kopie.xlsx, ImportTest.xlsx]
2023-07-13 added CAD
    [HEL-03-01001-00.SLDASM, HEL-03-01003-00.SLDASM, HEL-03-01006-00.SLDASM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]
2023-07-13 renamed assembly
2023-07-13 CAD files
2023-07-13 added widget to bill of materials
2023-07-13 updated BoM and description
    [ImportTest.xlsx]
2023-07-14 CAD updated
    [HEL-03-01009-00.SLDDRW, HEL-03-01010-00.SLDDRW, HEL-03-03000-00.SLDASM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]
2023-07-14 renamed main assembly
2023-07-14 cleaned up files
    [Helmoro_2_BoM_28-03-2023.xlsx, Helmoro_2_BoM_English­­_26-06-2023 - Kopie.xlsx, Helmoro_BoM_14-07-2023.xlsx]
2023-07-14 small changes in hw documentation
    [Helmoro_2_BoM_English­­_26-06-2023 - Kopie.xlsx, ImportTest.xlsx]
2023-07-14 cad update
2023-07-14 new embedding
    [Helmoro_BoM_14-07-2023.xlsx]
2023-07-25 new cad files and instructions
    [HEL-03-01001-00.SLDASM, HEL-03-01003-00.SLDASM, HEL-03-01006-00.SLDASM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]
2023-07-25 new cad
2023-07-25 updated BoM and get started
    [Helmoro_BoM_14-07-2023.xlsx, Helmoro_BoM_electronics.xlsx, Helmoro_BoM_fasteners.xlsx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]
2023-07-25 added all stl and step files of parts
2023-07-25 Use Git LFS for large CAD file
2023-07-25 all step and stl files
    [HEL-03-01000-02_Main_Assembly.step, HEL-03-01003-00.step, HEL-03-01005-00.step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]
2023-07-26 move cad files
    [HEL-03-01000-02_Main_Assembly.step, HEL-03-01001-00.SLDASM, HEL-03-01003-00.SLDASM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]
2023-07-26 small changes
    [Helmoro_BoM_sheet_metals.xlsx]
2023-07-26 updates before new cad files
    [Helmoro_BoM.xlsx, Helmoro_BoM_electronics.xlsx, Helmoro_BoM_fasteners.xlsx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]
2023-07-26 new cad files
    [HEL-01-01000-01.step, HEL-03-01000-02_Main_Assembly.step, HEL-03-01003-00.SLDASM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]
2023-07-26 ready for first publish
    [Helmoro_BoM_generative_parts.xlsx]
2023-07-27 fixed assembly lists
2024-04-05 Landing Page updated and tools moved to HW instructions (#44)
    * Landing Page updated and tools moved to HW instructions
    * add google analytics
2024-04-12 Fix landing page and doc (#53)
    * changes on landingpage - closes #48
    * more concise description section making it less overlap - closes #50
2024-05-24 corrected typos
    [ros_architecture_realrobot.xml]
2025-02-21 Update documentation for ROS 2 transition
    Update documentation for ROS 2 transition (#65)
    * Reorganized structure
    * Revised outdated content
    [HEL-01-01000-01.step, HEL-01-01000-02 - HEL-03-01001-00-1 HEL-04-03000-01-1.STL, HEL-01-01000-02 - HEL-03-01001-00-1 HEL-06-01000-01-1.STL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]
